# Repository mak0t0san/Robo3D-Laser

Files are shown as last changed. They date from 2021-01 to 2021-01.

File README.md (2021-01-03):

# Robo3D-Laser

## WARNING!!! 
* ### Working with lasers can be dangerous.  Wear proper eye protection! 
* ### Using high power lasers to engrave or cut will create smoke and fumes. Use in a well ventilated area.
* ### This guide is provided without any guarantees or warranties.  I am not responsible for any property damage or injuries.
* ### I am not a laser expert. Please read up on safety guidelines for Class IIIb lasers.

<br>
<br>
This is a guide to attaching the Creality (or Comgrow) laser head kit to the Robo 3D R1.  The laser head was designed to be able to quicky be mounted and removed via the magnets on it.  The R1 does not have a place to quickly mount this laser head kit.  What I have done is remove the extruder assembly from the printer and replace it with a laser module.

The laser module can be purchased here (affiliate link, would appreciate ordering from this link especially if you found this guide helpful).
https://amzn.to/3hBcbAK

Before removing your extruder, make sure you are able to print this mount for the laser module: https://github.com/mak0t0san/Robo3D-Laser/blob/main/3D%20Models/Robo3D%20Laser%20Mount.stl

<dl>
  <dt><h2>Extruder Removal</h2></dt>
  <dd>Disconnect all the wires going to the extruder assembly. This includes the cable for the stepper motor, thermistor, and heater cartrdige. You can also remove the part cooling fan and the heatsink fan as these won't be needed.  Then, unscrew the two bolts holding the extruder plate on.  You can use a small Phillips screwdriver from the bottom of the extruder plate. You might need some pliers to hold the nuts on the top in place.</dd>
  <dt><h2>Laser assembly</h2></dt>
  <dd>
  <ol>
  <li>
  Attach the laser module to the mount that you downloaded and printed.  You'll need a couple of short M3 screws.  I've found that only 2 screws are needed to hold it securely but you're welcome to use 4. </li>
  <li>Then place the mount into the R1 where the extruder was. You'll be able to attach this with the 2 nuts and bolts that were holding the extruder in place before. 
  </li>
  <li>
  Remove the bottom cover from the R1. We'll need to get to the board. The R1 has a modified version of the RAMPS 1.4 board (which is mounted to an Arduino). Once you have the bottom cover off, locate the fan wire.  It's a plug towards the top-right (if you laid your R1 on the left side) of the board and is labeled "FAN". Disconnect the fan from here and then plug in the laser module.  The connector on the laser module is not the same as the fan plug but it will fit in place as the pin size and spacing is the same. Make sure to match up the polarity correctly (Red +, Black -).
  </li>
  </ol>
  <div style="margin-left:auto;margin-right:auto">
  <a href="https://raw.githubusercontent.com/mak0t0san/Robo3D-Laser/main/assets/fan-connector.png" >
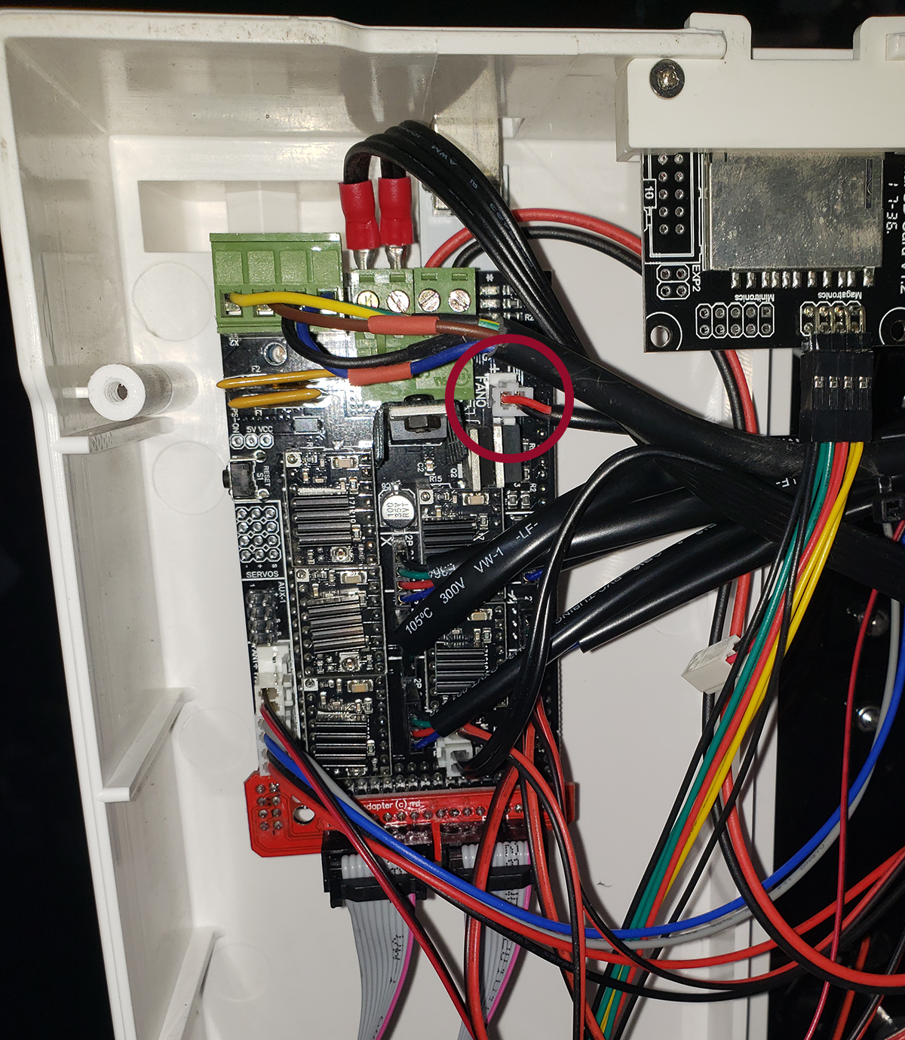
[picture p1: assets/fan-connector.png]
Fan connector
  
  </a>
  </div>
  </dd>
  <dt><h2>Usage</h2></dt>
  <dd>
  <p>
  This laser module was designed to be able to be added and removed quickly by swapping out the fan for the laser.  At this point, you should be good to go to use the laser, just make sure that the software that you're using uses <code>M106</code> and <code>M107</code> to turn on and off the laser instead of <code>M3</code> and <code>M5</code>. 
  </p>
  <p>
  However, using this setup without updating your firmware will limit you quite a bit.  The default firmware doesn't support arc commands (<code>G2</code> or <code>G3</code>) and also doesn't support inline laser power.  You'll be limited to what you can use the laser for.  <br>
  I have created a configuration for Marlin that will allow your R1 to act like a proper laser engraver.
  </p>
  <p>
  There are a couple of important features that have been enabled. Mainly, support for G2 and G3 arc commands, and <code>LASER_POWER_INLINE</code>.  This allows <code>G1</code> commands to specify laser power via the <code>S</code> parameter. This enables the planner to change the laser output and continue to move smoothly.
  </p>
  <p>
  In the configuration file, I specify the board type to be <code>BOARD_RAMPS_14_SF</code>. This means RAMPS 1.4 Spindle/Fan.  The default one is <code>BOARD_RAMPS_14_EFB</code> (<u>E</u>xtruder <u>F</u>an <u>B</u>ed). Instead of a spindle, we'll be using a laser.
  </p>
  <p>
  Also of note: Many laser modules have a separate input for TTL PWM input.  With TTL input, the PWM signal would be connected to one of the 5V output pins from the Arduino, such as the ones available in the servo pins.  The laser module that I'm using and referenced in this guide does not have a separate PWM input.  We'll be using the 12V output from the FAN connector which is driven by a MOSFET.
  </p>
  <p>
  In the configuration file, please make sure to configure your display type correctly. The R1 does not come with a display so if you want one, you'll need to add one.  I'm using a FYSETC graphical display and that's what I've got configure. If you're using a RepRap graphical display, please make sure to update your configuration to reflect that.  You can also use this without a display and hooked up via USB however I prefer to have a stand-alone machine that doesn't require another computer plugged into it.
  </p>
  </dd>
  <dt>
  <h2>Notes</h2>
  </dt>
  <dd>
I've found that engraving high resolution raster images with an 8-bit Arduino running at 16MHz has its limitations. It will stutter when printing at higher speeds and compete with resources when the display is refreshing.  If you're going to be engraving at higher speeds, I would highly recommend switching to a faster 32-bit board.
  </dd>
</dl>

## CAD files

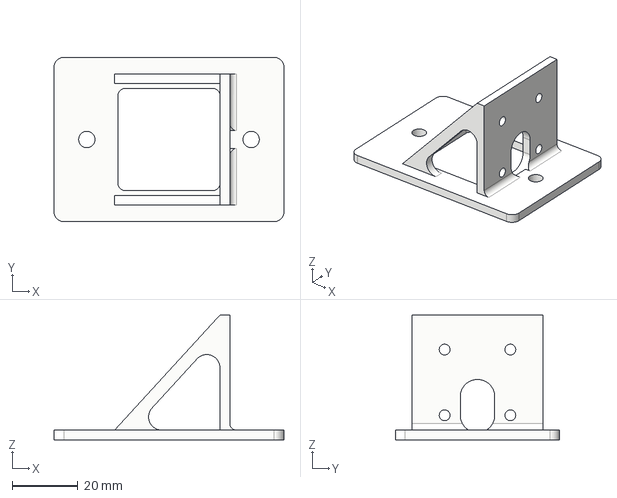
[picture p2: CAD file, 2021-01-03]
3D Models/Robo3D Laser Mount.step
70.0 x 50.0 x 38.0 mm

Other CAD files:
3D Models/Robo3D Laser Mount.stl

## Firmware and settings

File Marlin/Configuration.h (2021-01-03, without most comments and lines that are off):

#pragma once
#define CONFIGURATION_H_VERSION 020008
#define STRING_CONFIG_H_AUTHOR "(Makoto Schoppert, Robo3D R1+)" // Who made the changes.
#define SHOW_BOOTSCREEN
#define SERIAL_PORT 0
#define BAUDRATE 250000
  #define MOTHERBOARD BOARD_RAMPS_14_SF
#define CUSTOM_MACHINE_NAME "Robo 3D R1+"
#define EXTRUDERS 0
#define DEFAULT_NOMINAL_FILAMENT_DIA 1.75
#define TEMP_SENSOR_0 0
#define TEMP_SENSOR_1 0
#define TEMP_SENSOR_2 0
#define TEMP_SENSOR_3 0
#define TEMP_SENSOR_4 0
#define TEMP_SENSOR_5 0
#define TEMP_SENSOR_6 0
#define TEMP_SENSOR_7 0
#define TEMP_SENSOR_BED 0 // ncrmro
#define TEMP_SENSOR_PROBE 0
#define TEMP_SENSOR_CHAMBER 0
#define DUMMY_THERMISTOR_998_VALUE 25
#define DUMMY_THERMISTOR_999_VALUE 100
#define MAX_REDUNDANT_TEMP_SENSOR_DIFF 10
#define TEMP_RESIDENCY_TIME     10  // (seconds) Time to wait for hotend to "settle" in M109
#define TEMP_WINDOW              1  // (°C) Temperature proximity for the "temperature reached" timer
#define TEMP_HYSTERESIS          3  // (°C) Temperature proximity considered "close enough" to the target
#define TEMP_BED_RESIDENCY_TIME 10  // (seconds) Time to wait for bed to "settle" in M190
#define TEMP_BED_WINDOW          1  // (°C) Temperature proximity for the "temperature reached" timer
#define TEMP_BED_HYSTERESIS      3  // (°C) Temperature proximity considered "close enough" to the target
#define HEATER_0_MINTEMP   5
#define HEATER_1_MINTEMP   5
#define HEATER_2_MINTEMP   5
#define HEATER_3_MINTEMP   5
#define HEATER_4_MINTEMP   5
#define HEATER_5_MINTEMP   5
#define HEATER_6_MINTEMP   5
#define HEATER_7_MINTEMP   5
#define BED_MINTEMP        5
#define HEATER_0_MAXTEMP 275
#define HEATER_1_MAXTEMP 275
#define HEATER_2_MAXTEMP 275
#define HEATER_3_MAXTEMP 275
#define HEATER_4_MAXTEMP 275
#define HEATER_5_MAXTEMP 275
#define HEATER_6_MAXTEMP 275
#define HEATER_7_MAXTEMP 275
#define BED_MAXTEMP      150
#define BANG_MAX 255     // Limits current to nozzle while in bang-bang mode; 255=full current
#define PID_MAX BANG_MAX // Limits current to nozzle while PID is active (see PID_FUNCTIONAL_RANGE below); 255=full current
#define PID_K1 0.95      // Smoothing factor within any PID loop
#define MAX_BED_POWER 255 // limits duty cycle to bed; 255=full current
#define PREVENT_COLD_EXTRUSION
#define EXTRUDE_MINTEMP 170
#define PREVENT_LENGTHY_EXTRUDE
#define EXTRUDE_MAXLENGTH 200
#define THERMAL_PROTECTION_HOTENDS // Enable thermal protection for all extruders
#define THERMAL_PROTECTION_BED     // Enable thermal protection for the heated bed
#define THERMAL_PROTECTION_CHAMBER // Enable thermal protection for the heated chamber
#define USE_XMIN_PLUG
#define USE_YMIN_PLUG
#define USE_ZMIN_PLUG
#define ENDSTOPPULLUPS
#define X_MIN_ENDSTOP_INVERTING false // Set to true to invert the logic of the endstop.
#define Y_MIN_ENDSTOP_INVERTING false // Set to true to invert the logic of the endstop.
#define Z_MIN_ENDSTOP_INVERTING true // Set to true to invert the logic of the endstop.
#define X_MAX_ENDSTOP_INVERTING false // Set to true to invert the logic of the endstop.
#define Y_MAX_ENDSTOP_INVERTING false // Set to true to invert the logic of the endstop.
#define Z_MAX_ENDSTOP_INVERTING false // Set to true to invert the logic of the endstop.
#define Z_MIN_PROBE_ENDSTOP_INVERTING true // Set to true to invert the logic of the probe.
#define X_DRIVER_TYPE  A4988
#define Y_DRIVER_TYPE  A4988
#define Z_DRIVER_TYPE  A4988
#define Z2_DRIVER_TYPE A4988
#define DEFAULT_AXIS_STEPS_PER_UNIT   { 80, 80, 800, 815 }
#define DEFAULT_MAX_FEEDRATE          { 300, 300, 5, 25 }
#define DEFAULT_MAX_ACCELERATION      { 6000, 6000, 100, 10000 }
#define DEFAULT_ACCELERATION          6000    // X, Y, Z and E acceleration for printing moves
#define DEFAULT_RETRACT_ACCELERATION  3000    // E acceleration for retracts
#define DEFAULT_TRAVEL_ACCELERATION   3000    // X, Y, Z acceleration for travel (non printing) moves
#define DEFAULT_EJERK    5.0  // May be used by Linear Advance
  #define JUNCTION_DEVIATION_MM 0.013 // (mm) Distance from real junction edge
  #define JD_HANDLE_SMALL_SEGMENTS    // Use curvature estimation instead of just the junction angle
#define S_CURVE_ACCELERATION
#define Z_MIN_PROBE_USES_Z_MIN_ENDSTOP_PIN
#define NOZZLE_AS_PROBE
#define NOZZLE_TO_PROBE_OFFSET { 0, 0, 1.20 }
#define PROBING_MARGIN 10
#define XY_PROBE_SPEED (133*60)
#define Z_PROBE_SPEED_FAST (4*60)
#define Z_PROBE_SPEED_SLOW (Z_PROBE_SPEED_FAST / 2)
#define Z_CLEARANCE_DEPLOY_PROBE   10 // Z Clearance for Deploy/Stow
#define Z_CLEARANCE_BETWEEN_PROBES  5 // Z Clearance between probe points
#define Z_CLEARANCE_MULTI_PROBE     5 // Z Clearance between multiple probes
#define Z_PROBE_LOW_POINT          -2 // Farthest distance below the trigger-point to go before stopping
#define Z_PROBE_OFFSET_RANGE_MIN -20
#define Z_PROBE_OFFSET_RANGE_MAX 20
#define X_ENABLE_ON 0
#define Y_ENABLE_ON 0
#define Z_ENABLE_ON 0
#define E_ENABLE_ON 0 // For all extruders
#define DISABLE_X false
#define DISABLE_Y false
#define DISABLE_Z false
#define DISABLE_E false             // Disable the extruder when not stepping
#define DISABLE_INACTIVE_EXTRUDER   // Keep only the active extruder enabled
#define INVERT_X_DIR true
#define INVERT_Y_DIR false
#define INVERT_Z_DIR true
#define INVERT_E0_DIR true
#define INVERT_E1_DIR false
#define INVERT_E2_DIR false
#define INVERT_E3_DIR false
#define INVERT_E4_DIR false
#define INVERT_E5_DIR false
#define INVERT_E6_DIR false
#define INVERT_E7_DIR false
#define Z_HOMING_HEIGHT  4      // (mm) Minimal Z height before homing (G28) for Z clearance above the bed, clamps, ...
#define Z_AFTER_HOMING  10      // (mm) Height to move to after homing Z
#define X_HOME_DIR -1
#define Y_HOME_DIR -1
#define Z_HOME_DIR -1
#define X_BED_SIZE 220
#define Y_BED_SIZE 220
#define X_MIN_POS 0
#define Y_MIN_POS 0
#define Z_MIN_POS 0
#define X_MAX_POS X_BED_SIZE
#define Y_MAX_POS Y_BED_SIZE
#define Z_MAX_POS 200
#define MIN_SOFTWARE_ENDSTOPS true
  #define MIN_SOFTWARE_ENDSTOP_X
  #define MIN_SOFTWARE_ENDSTOP_Y
#define MAX_SOFTWARE_ENDSTOPS true
  #define MAX_SOFTWARE_ENDSTOP_X
  #define MAX_SOFTWARE_ENDSTOP_Y
  #define SOFT_ENDSTOPS_MENU_ITEM  // Enable/Disable software endstops from the LCD
#define AUTO_BED_LEVELING_LINEAR
#define RESTORE_LEVELING_AFTER_G28
  #define GRID_MAX_POINTS_X 2
  #define GRID_MAX_POINTS_Y GRID_MAX_POINTS_X
#define Z_SAFE_HOMING
  #define Z_SAFE_HOMING_X_POINT X_CENTER  // X point for Z homing
  #define Z_SAFE_HOMING_Y_POINT Y_CENTER  // Y point for Z homing
#define HOMING_FEEDRATE_MM_M { (50*60), (50*60), (4*60) }
#define VALIDATE_HOMING_ENDSTOPS
#define EEPROM_SETTINGS     // Persistent storage with M500 and M501
#define EEPROM_CHITCHAT       // Give feedback on EEPROM commands. Disable to save PROGMEM.
#define EEPROM_BOOT_SILENT    // Keep M503 quiet and only give errors during first load
#define HOST_KEEPALIVE_FEATURE        // Disable this if your host doesn't like keepalive messages
#define DEFAULT_KEEPALIVE_INTERVAL 2  // Number of seconds between "busy" messages. Set with M113.
#define BUSY_WHILE_HEATING            // Some hosts require "busy" messages even during heating
#define PREHEAT_1_LABEL       "PLA"
#define PREHEAT_1_TEMP_HOTEND 200
#define PREHEAT_1_TEMP_BED     60
#define PREHEAT_1_FAN_SPEED     0 // Value from 0 to 255
#define PREHEAT_2_LABEL       "ABS"
#define PREHEAT_2_TEMP_HOTEND 240
#define PREHEAT_2_TEMP_BED    110
#define PREHEAT_2_FAN_SPEED     0 // Value from 0 to 255
#define PRINTJOB_TIMER_AUTOSTART
#define PRINTCOUNTER
#define LCD_LANGUAGE en
#define DISPLAY_CHARSET_HD44780 JAPANESE
#define LCD_INFO_SCREEN_STYLE 0
#define SDSUPPORT
#define ENCODER_PULSES_PER_STEP 2
#define INDIVIDUAL_AXIS_HOMING_MENU
#define SPEAKER
#define FYSETC_MINI_12864_2_1    // Type A/B. NeoPixel RGB Backlight
#define SOFT_PWM_SCALE 0
#define NEOPIXEL_BRIGHTNESS 255
#define SERVO_DELAY { 300 }

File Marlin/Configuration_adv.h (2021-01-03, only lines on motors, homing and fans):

#define E0_AUTO_FAN_PIN -1
#define E1_AUTO_FAN_PIN -1
#define E2_AUTO_FAN_PIN -1
#define E3_AUTO_FAN_PIN -1
#define E4_AUTO_FAN_PIN -1
#define E5_AUTO_FAN_PIN -1
#define E6_AUTO_FAN_PIN -1
#define E7_AUTO_FAN_PIN -1
#define CHAMBER_AUTO_FAN_PIN -1
#define HOMING_BUMP_MM      { 5, 5, 2 }       // (mm) Backoff from endstops after first bump
#define HOMING_BUMP_DIVISOR { 2, 2, 4 }       // Re-Bump Speed Divisor (Divides the Homing Feedrate)
  #define HOME_AFTER_G34
#define MICROSTEP_MODES { 16, 16, 16, 16, 16, 16 } // [1,2,4,8,16]

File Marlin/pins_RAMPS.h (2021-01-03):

/**
 * Marlin 3D Printer Firmware
 * Copyright (c) 2020 MarlinFirmware [https://github.com/MarlinFirmware/Marlin]
 *
 * Based on Sprinter and grbl.
 * Copyright (c) 2011 Camiel Gubbels / Erik van der Zalm
 *
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
 */
#pragma once

/**
 * Arduino Mega with RAMPS v1.4 (or v1.3) pin assignments
 *
 * Applies to the following boards:
 *
 *  RAMPS_14_EFB (Hotend, Fan, Bed)
 *  RAMPS_14_EEB (Hotend0, Hotend1, Bed)
 *  RAMPS_14_EFF (Hotend, Fan0, Fan1)
 *  RAMPS_14_EEF (Hotend0, Hotend1, Fan)
 *  RAMPS_14_SF  (Spindle, Controller Fan)
 *
 *  RAMPS_13_EFB (Hotend, Fan, Bed)
 *  RAMPS_13_EEB (Hotend0, Hotend1, Bed)
 *  RAMPS_13_EFF (Hotend, Fan0, Fan1)
 *  RAMPS_13_EEF (Hotend0, Hotend1, Fan)
 *  RAMPS_13_SF  (Spindle, Controller Fan)
 *
 *  Other pins_MYBOARD.h files may override these defaults
 *
 *  Differences between
 *  RAMPS_13 | RAMPS_14
 *         7 | 11
 */

#ifdef TARGET_LPC1768
  #error "Oops! Set MOTHERBOARD to an LPC1768-based board when building for LPC1768."
#elif defined(__STM32F1__)
  #error "Oops! Set MOTHERBOARD to an STM32F1-based board when building for STM32F1."
#endif

#if NOT_TARGET(IS_RAMPS_SMART, IS_RAMPS_DUO, IS_RAMPS4DUE, TARGET_LPC1768, __AVR_ATmega1280__, __AVR_ATmega2560__)
  #error "Oops! Select 'Arduino/Genuino Mega or Mega 2560' (or other appropriate target) in 'Tools > Board.'"
#endif

// Custom flags and defines for the build
//#define BOARD_CUSTOM_BUILD_FLAGS -D__FOO__

#ifndef BOARD_INFO_NAME
  #define BOARD_INFO_NAME "RAMPS 1.4"
#endif

//
// Servos
//
#ifndef SERVO0_PIN
  #ifdef IS_RAMPS_13
    #define SERVO0_PIN                         7
  #else
    #define SERVO0_PIN                        11
  #endif
#endif
#ifndef SERVO1_PIN
  #define SERVO1_PIN                           6
#endif
#ifndef SERVO2_PIN
  #define SERVO2_PIN                           5
#endif
#ifndef SERVO3_PIN
  #define SERVO3_PIN                           4
#endif

//
// Limit Switches
//
#ifndef X_STOP_PIN
  #ifndef X_MIN_PIN
    #define X_MIN_PIN                          3
  #endif
  #ifndef X_MAX_PIN
    #define X_MAX_PIN                          2
  #endif
#endif
#ifndef Y_STOP_PIN
  #ifndef Y_MIN_PIN
    #define Y_MIN_PIN                         14
  #endif
  #ifndef Y_MAX_PIN
    #define Y_MAX_PIN                         15
  #endif
#endif
#ifndef Z_STOP_PIN
  #ifndef Z_MIN_PIN
    #define Z_MIN_PIN                         18
  #endif
  #ifndef Z_MAX_PIN
    #define Z_MAX_PIN                         19
  #endif
#endif

//
// Z Probe (when not Z_MIN_PIN)
//
#ifndef Z_MIN_PROBE_PIN
  #define Z_MIN_PROBE_PIN                     32
#endif

//
// Steppers
//
#define X_STEP_PIN                            54
#define X_DIR_PIN                             55
#define X_ENABLE_PIN                          38
#ifndef X_CS_PIN
  #define X_CS_PIN                            53
#endif

#define Y_STEP_PIN                            60
#define Y_DIR_PIN                             61
#define Y_ENABLE_PIN                          56
#ifndef Y_CS_PIN
  #define Y_CS_PIN                            49
#endif

#ifndef Z_STEP_PIN
  #define Z_STEP_PIN                          46
#endif
#define Z_DIR_PIN                             48
#define Z_ENABLE_PIN                          62
#ifndef Z_CS_PIN
  #define Z_CS_PIN                            40
#endif

#define E0_STEP_PIN                           26
#define E0_DIR_PIN                            28
#define E0_ENABLE_PIN                         24
#ifndef E0_CS_PIN
  #define E0_CS_PIN                           42
#endif

#define E1_STEP_PIN                           36
#define E1_DIR_PIN                            34
#define E1_ENABLE_PIN                         30
#ifndef E1_CS_PIN
  #define E1_CS_PIN                           44
#endif

//
// Temperature Sensors
//
#ifndef TEMP_0_PIN
  #define TEMP_0_PIN                          13  // Analog Input
#endif
#ifndef TEMP_1_PIN
  #define TEMP_1_PIN                          15  // Analog Input
#endif
#ifndef TEMP_BED_PIN
  #define TEMP_BED_PIN                        14  // Analog Input
#endif

//
// SPI for Max6675 or Max31855 Thermocouple
//
#ifndef MAX6675_SS_PIN
  #define MAX6675_SS_PIN                      66  // Don't use 53 if using Display/SD card (SDSS) or 49 (SD_DETECT_PIN)
#endif

//
// Augmentation for auto-assigning RAMPS plugs
//
#if NONE(IS_RAMPS_EEB, IS_RAMPS_EEF, IS_RAMPS_EFB, IS_RAMPS_EFF, IS_RAMPS_SF) && !PIN_EXISTS(MOSFET_D)
  #if HAS_MULTI_HOTEND
    #if TEMP_SENSOR_BED
      #define IS_RAMPS_EEB
    #else
      #define IS_RAMPS_EEF
    #endif
  #elif TEMP_SENSOR_BED
    #define IS_RAMPS_EFB
  #else
    #define IS_RAMPS_EFF
  #endif
#endif

//
// Heaters / Fans
//
#ifndef MOSFET_D_PIN
  #define MOSFET_D_PIN                        -1
#endif
#ifndef RAMPS_D8_PIN
  #define RAMPS_D8_PIN                         8
#endif
#ifndef RAMPS_D9_PIN
  #define RAMPS_D9_PIN                         9
#endif
#ifndef RAMPS_D10_PIN
  #define RAMPS_D10_PIN                       10
#endif
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

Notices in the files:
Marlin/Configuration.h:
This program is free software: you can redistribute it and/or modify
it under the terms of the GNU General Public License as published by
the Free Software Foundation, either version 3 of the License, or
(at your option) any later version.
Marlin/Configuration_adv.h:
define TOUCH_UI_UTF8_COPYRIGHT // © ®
